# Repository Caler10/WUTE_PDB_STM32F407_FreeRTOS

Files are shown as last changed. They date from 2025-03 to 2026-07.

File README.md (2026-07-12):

# 针对WUTE车队电动方程式赛车开发的智能低压配电板 PDB

# 关于本项目

一款本人设计开发的基于STM32F4+FreeRTOS开发的智能低压配电板(PDB,Power Delivery Board)，具体功能如下：

1. 支持多路低压配电过流保护与诊断（基于智能高边驱动芯片，取代保险丝）
2. 支持对接入设备实现配电控制与管理，实现智能化配电功能（基于智能高边驱动芯片，取代继电器）
3. 负责赛车车身风扇、水泵、尾灯、蜂鸣器、DRS等设备的控制
4. 接收并解析来自VCU的配电CAN报文指令和来自仪表的DRS启停CAN报文，同时发送各路配电诊断数据、各车身设备启停状态至CAN总线
5. 集成DCDC继电器、激活继电器
6. 支持过流保护、反接保护、TVS保护、过压保护等多项安全功能

# 设计说明

## 硬件说明

因整车低压配电需要的载流较大，担心智能低压配电板由于设计缺陷导致需要重新设计和打板，为降低开发成本，驱动电路和控制电路采用分板设计（核心板+底板）

智能低压配电板架构图如下：

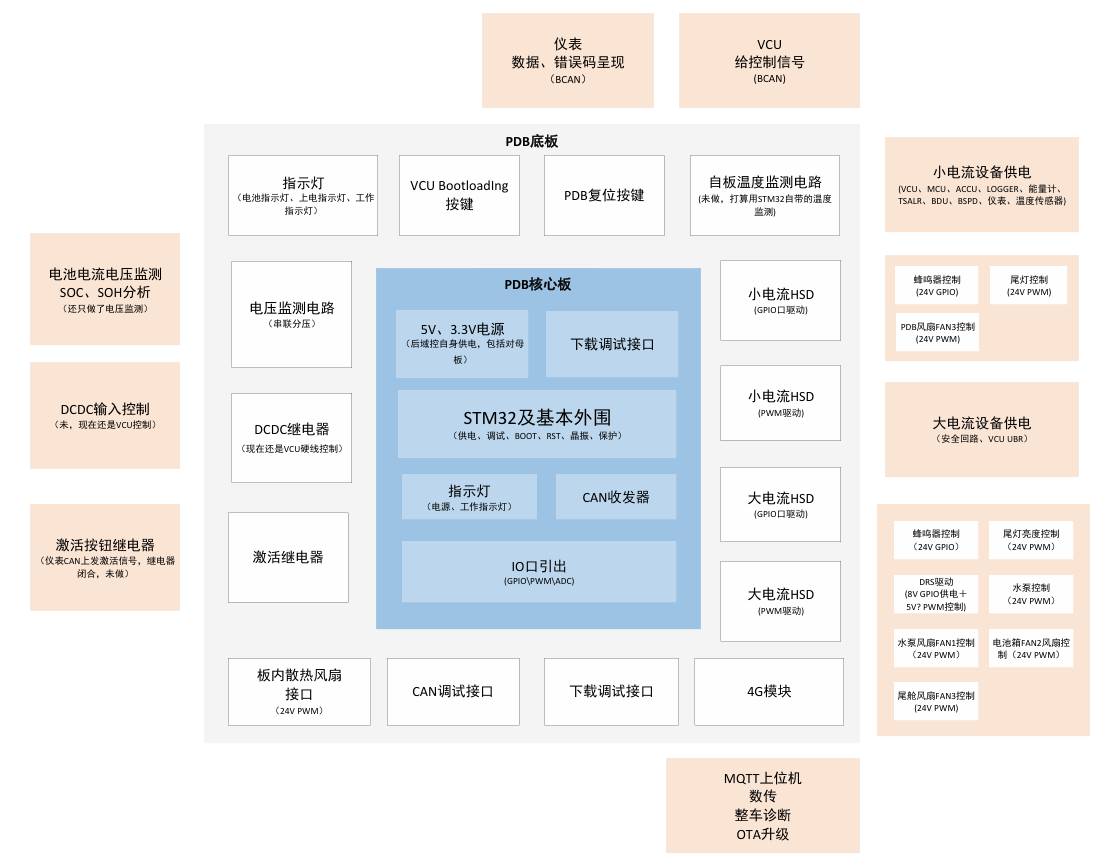
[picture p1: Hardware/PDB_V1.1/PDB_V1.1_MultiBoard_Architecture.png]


### PDB叠板设计

该项目硬件采用Altium Designer开发，PDB的核心板和底板之间采用板对板连接器连接

PDB_V1.0集成了OLED实时诊断数据显示，但是观察灵活性不够，因此PDB_V1.1取消了OLED，集成了4G数传功能，方便远程监测赛车配电情况，另外PDB_V1.1在底板增加了烧录、CAN调试接口，并优化了配电载流走线、修复了一些器件PCB封装问题

PDB_V1.0_MultiBoard：

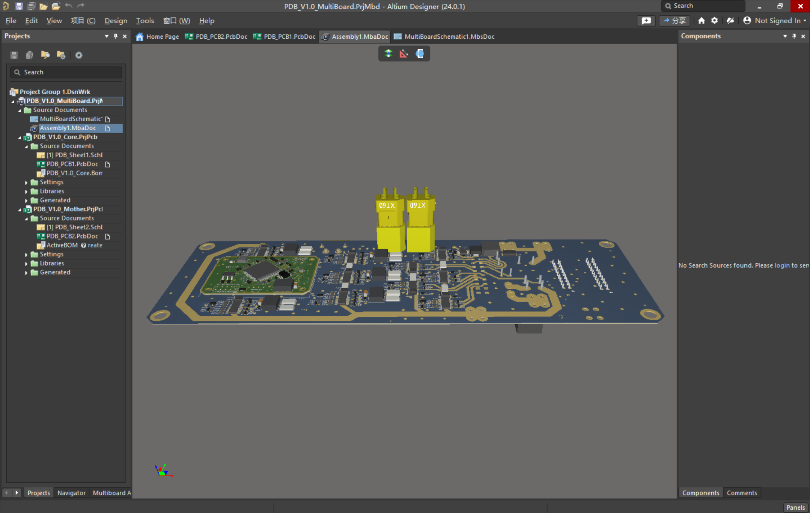
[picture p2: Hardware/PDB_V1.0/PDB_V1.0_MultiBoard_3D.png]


PDB_V1.1_MultiBoard：

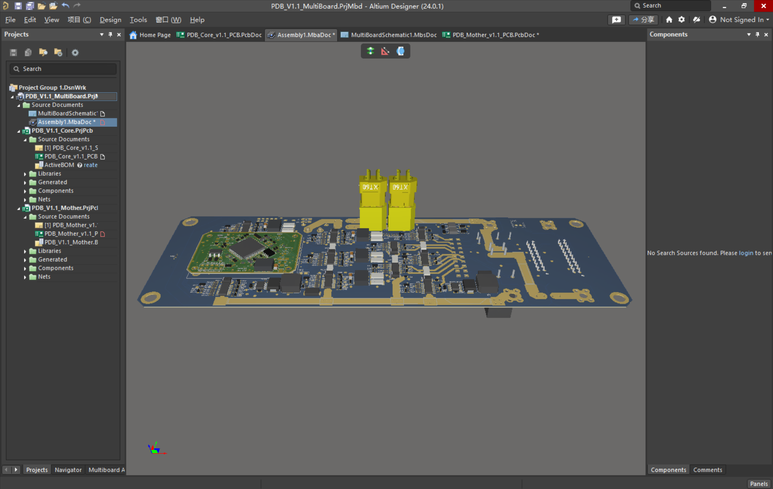
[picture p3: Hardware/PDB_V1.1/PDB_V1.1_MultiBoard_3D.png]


### PDB核心板设计

PDB_V1.0核心板：

V1.0核心板支持外接OLED，实现诊断数据实时显示

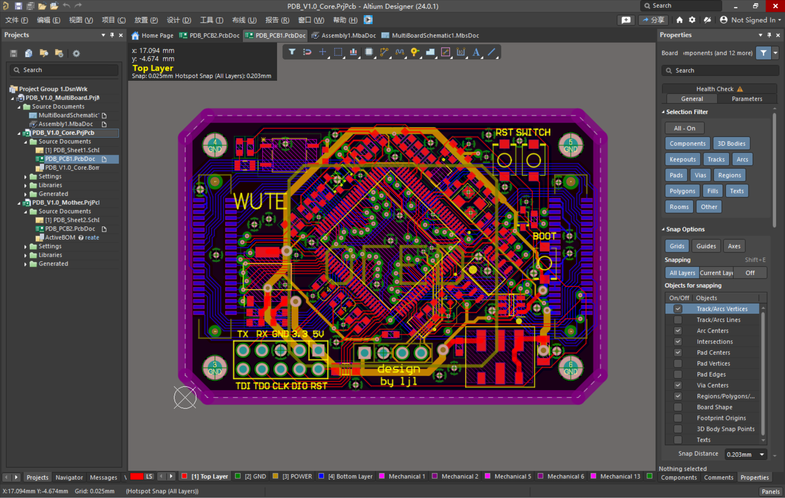
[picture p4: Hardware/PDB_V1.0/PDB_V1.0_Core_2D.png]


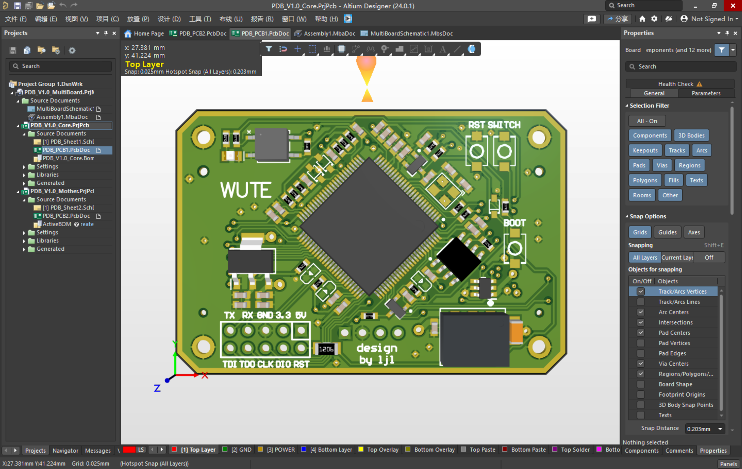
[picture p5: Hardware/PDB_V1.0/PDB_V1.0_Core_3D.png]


PDB_V1.1核心板：

V1.1核心板为兼容4G模块增加了3.3V至1.8V的电平转换模块，同时取消了OLED接口，另外相比V1.0版本增加了过流保护和反接保护电路

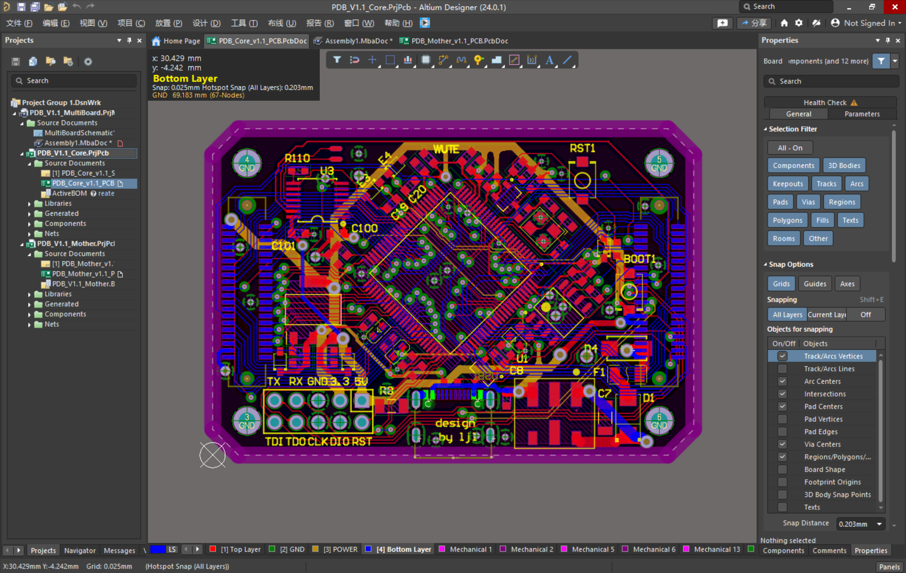
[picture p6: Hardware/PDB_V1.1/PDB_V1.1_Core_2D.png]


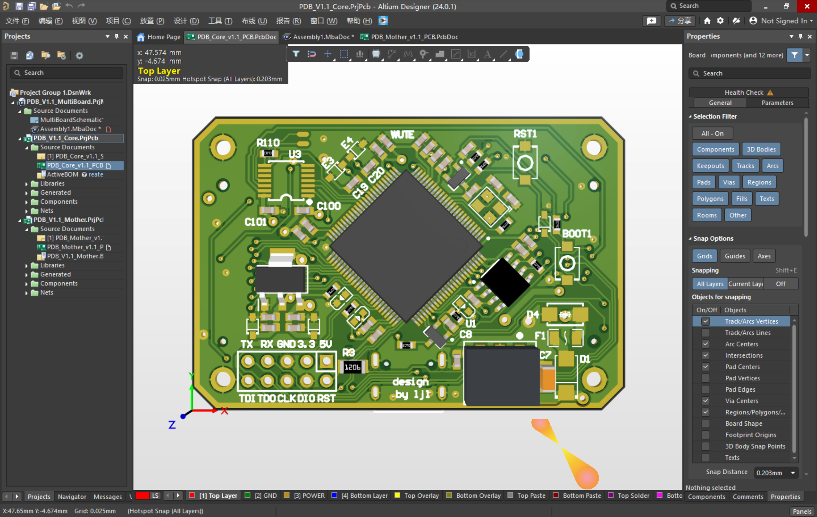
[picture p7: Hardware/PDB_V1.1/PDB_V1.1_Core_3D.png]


### PDB底板设计

PDB_V1.0底板：

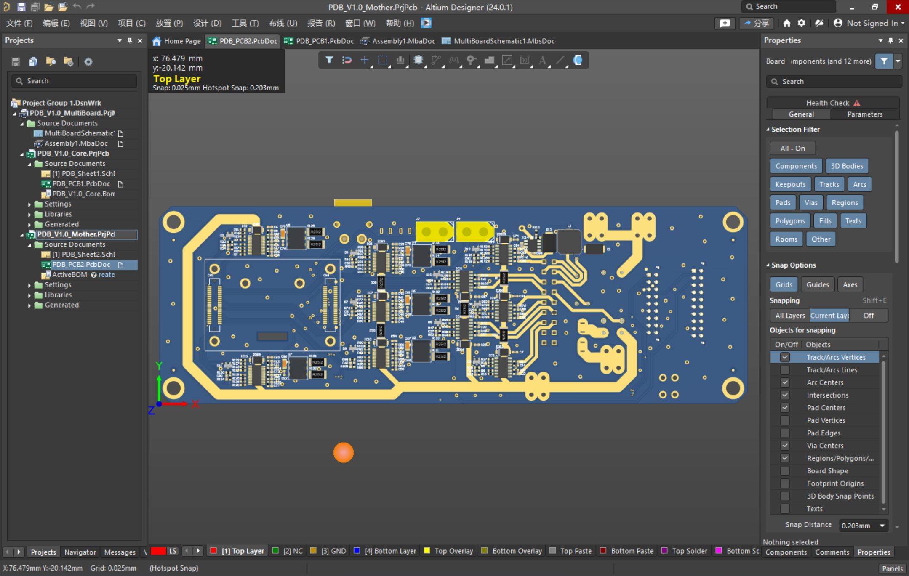
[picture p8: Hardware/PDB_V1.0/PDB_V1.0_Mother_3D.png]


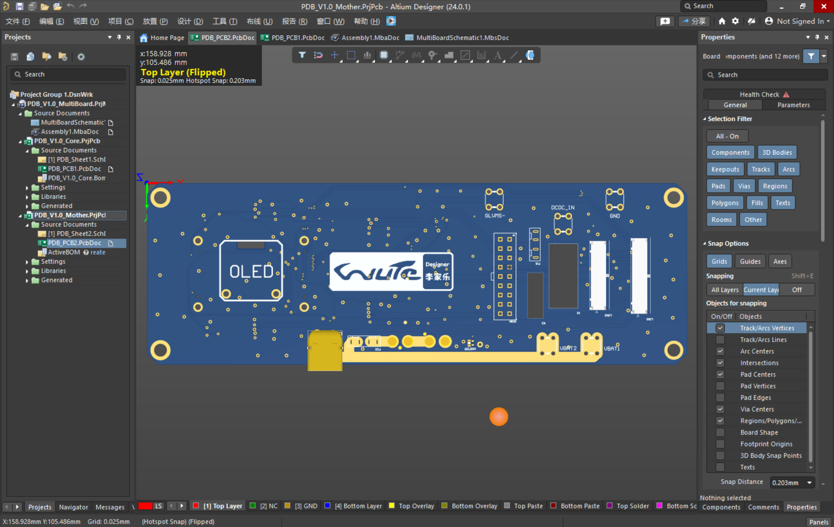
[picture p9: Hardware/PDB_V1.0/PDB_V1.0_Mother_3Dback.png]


PDB_V1.1底板：

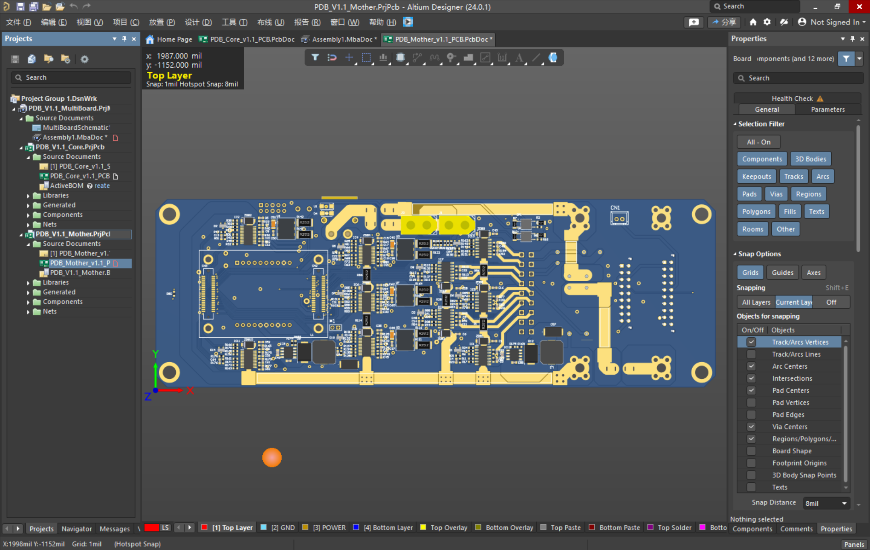
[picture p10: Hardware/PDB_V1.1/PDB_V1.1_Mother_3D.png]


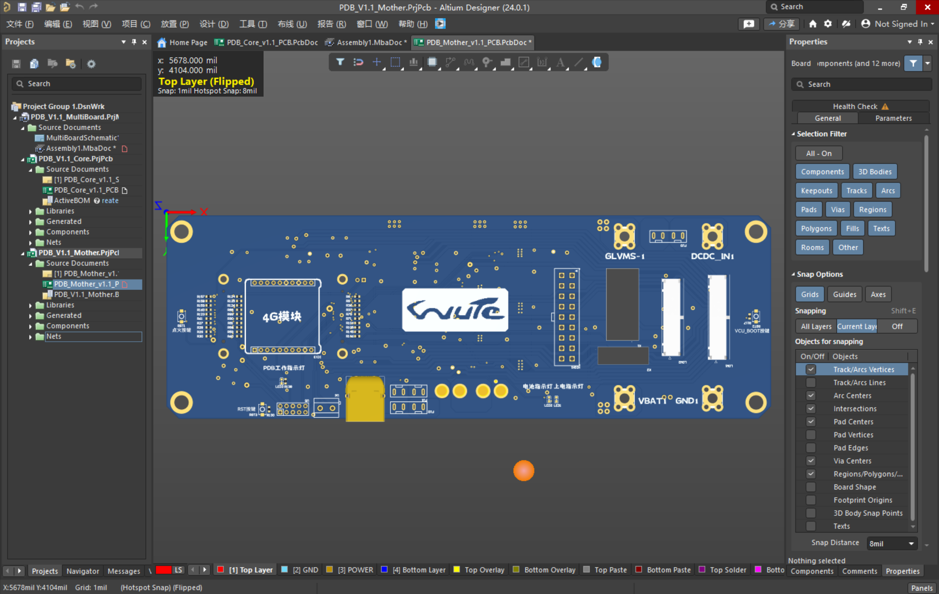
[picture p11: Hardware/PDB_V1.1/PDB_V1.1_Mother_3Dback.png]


## 软件说明

开发平台：STM32F407VET6

开发环境：STM32cubeMX+Keil

软件架构：基于CORE层+BSP层+FreeRTOS+APP层的架构开发

软件功能：

1. 智能高边驱动芯片HSD集群GPIO/PWM驱动
   
2. HSD诊断脚ADC+DMA中断采集与诊断分析
   
3. OLED IIC驱动与诊断可视化
   
4. CAN报文中断接收解析与诊断信息定时发送
   
5. 基于事件组/信号量/队列的任务间通信等

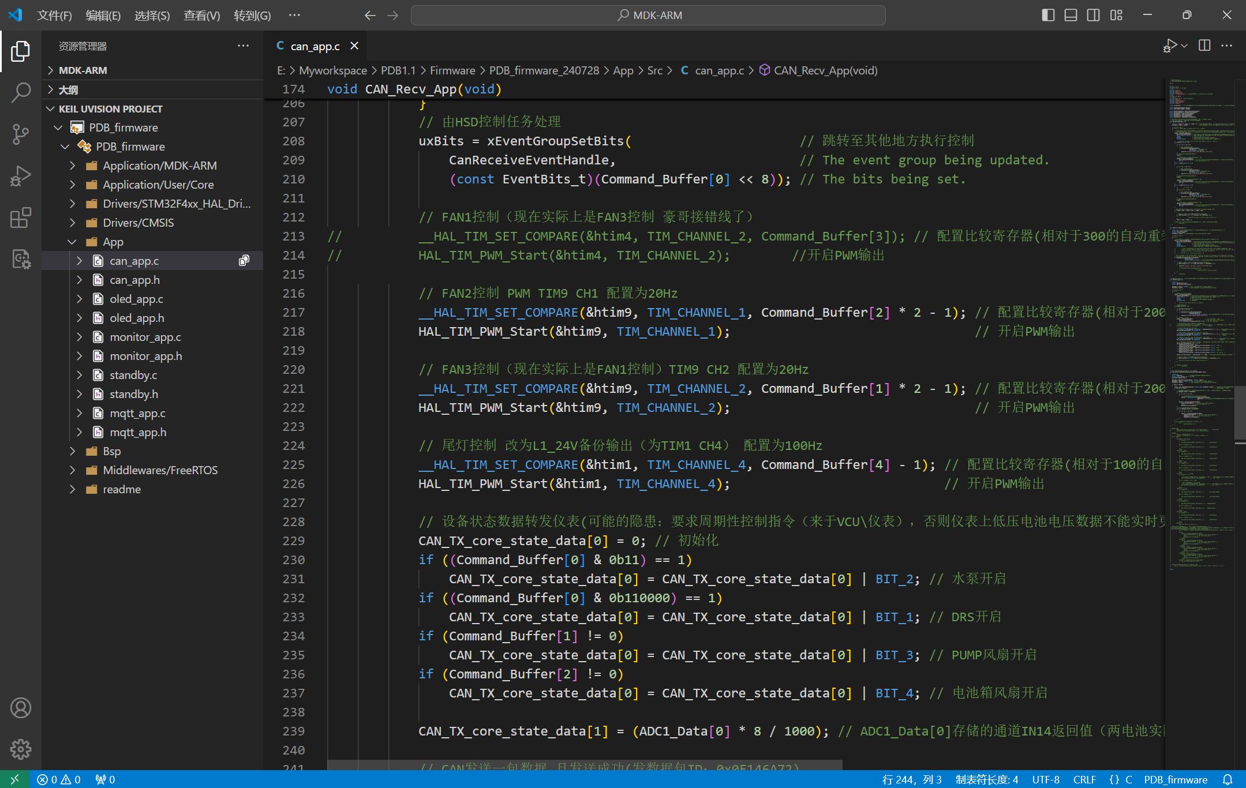
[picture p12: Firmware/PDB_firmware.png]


# 项目成果

该项目顺利完成开发并搭载在2024赛季E10赛车上，通过了累计50+小时的耐久测试，有效保障赛车低压系统配电安全同时实现了整车轻量化（采用HSD取代保险丝和继电器，实现配电盒整体减重约30%），并支撑E10赛车在2024年FSAE中国大学生电动方程式汽车大赛顺利完赛并取得全国季军。

智能低压配电板PDB实物图：



PDB和两块低压电池集成封装，布置在赛车尾部



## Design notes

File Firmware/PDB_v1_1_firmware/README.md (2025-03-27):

MX生成FreeRTOS版本（后面还有一个自己移植FreeRTOS版本）

由于电池VBAT始终向PDB供电，所以单片机不会关机，考虑读取PA0(上GLVMS为高，下GLVMS为低电平)

软件流程

当处于休眠时，监测到PA0上升沿唤醒

初始化阶段：
RST、上电后如果PA0读取非高电平（后可加其他条件，如CAN开始无应答、监听时），1分钟后进入休眠
如果PA0为高电平
    OLED开机界面启动
    CAN中断读取启动
    HSD所有输出开启
    OLED退出开机界面，进入指示状态

进入任务调度
    HSD1、HSD2诊断与分析（定时执行）[两队列：传出HSD诊断数据、报警信号；两事件：一出现报警信息，数据传输事件]（报过警的不丢,也显示，但说明过去式）
    电压监测与分析（定时执行）[两队列：电压监测数据、报警信号；两事件：一出现报警信息，数据传输事件]
    OLED监视（HSD电流检测数据来临事件启动）[收事件]
    CAN发送（HSD电流检测数据来临事件启动）[收事件]
    CAN接收（消息来临标志位启动）[收]
    HSD通道启停控制（CAN接收控制信号事件启动）[]
    DRS控制（CAN接收控制信号事件启动）[]
    准备与取消准备休眠（PA0 GPIO中断读取，为低电平后OLED指示将1分钟后进入休眠，当PA0回高电平时退出准备）[]
    休眠（由进入休眠事件启动，为低电平后倒计时1分钟后关闭LED、OLED，将PA0复用为唤醒引脚，配置寄存器进入休眠）[]

疑问：
有什么方式实现报警发过了不再发？
现在CAN接收标准帧和拓展帧都能收？

为什么OLED字符、图片数组声明、定义前要加const使其常数化（但是加了传入画图片函数里时会警告，所以去掉了）
小心多个任务读取同一个事件位时，一个读完了把厕所炸了其他的就上不了了

MX生成FreeRTOS的使用:
大部分FreeRTOS功能函数还要include对应文件后才能使用

HSD1handledEvent：存放HSD1组的完成诊断的相对输出口数据

CAN发尾灯信号，PDB控制
// 整合电压电流采集的两数据（数组）二维数组转一维数组，参考https://blog.csdn.net/m0_54158068/article/details/124275490

//有的地方set事件改为清理事件
uxBits = xEventGroupClearBits(
                                xEventGroup,  /* The event group being updated. */
                                BIT_0 | BIT_4 );/* The bits being cleared. */

  if( ( uxBits & ( BIT_0 | BIT_4 ) ) == ( BIT_0 | BIT_4 ) )
  {
      /* Both bit 0 and bit 4 were set before xEventGroupClearBits()
      was called.  Both will now be clear (not set). */
  }
  else if( ( uxBits & BIT_0 ) != 0 )
  {
      /* Bit 0 was set before xEventGroupClearBits() was called.  It will
      now be clear. */
  }
  else if( ( uxBits & BIT_4 ) != 0 )
  {
      /* Bit 4 was set before xEventGroupClearBits() was called.  It will
      now be clear. */
  }
  else
  {
      /* Neither bit 0 nor bit 4 were set in the first place. */
  }

20240524：
比20240413版本
解决了风扇无法控制的问题（CAN中断接收到后不能将数据完整地压入队列供CAN_Reseive函数接收处理）
取消诊断、诊断数据打包发送、错误发送功能（控制功耗）
删除CPU占用监测任务

20240704：
实现DRS的驱动
可以正常使用版本

20240728：
更新PDB指令报文的接收
实现尾灯、风扇PWM控制
PDB设备状态数据上CAN（给仪表）
实现惯导转发上CAN
实现4G模块驱动

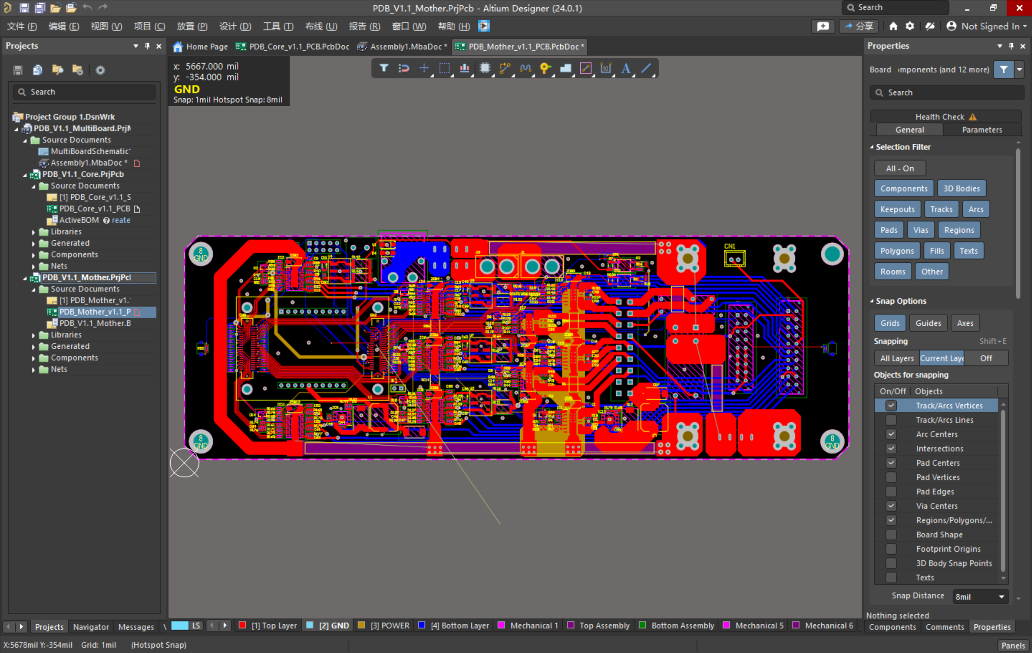
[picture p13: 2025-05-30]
Hardware/PDB_V1.1/PDB_V1.1_Mother_2D.png

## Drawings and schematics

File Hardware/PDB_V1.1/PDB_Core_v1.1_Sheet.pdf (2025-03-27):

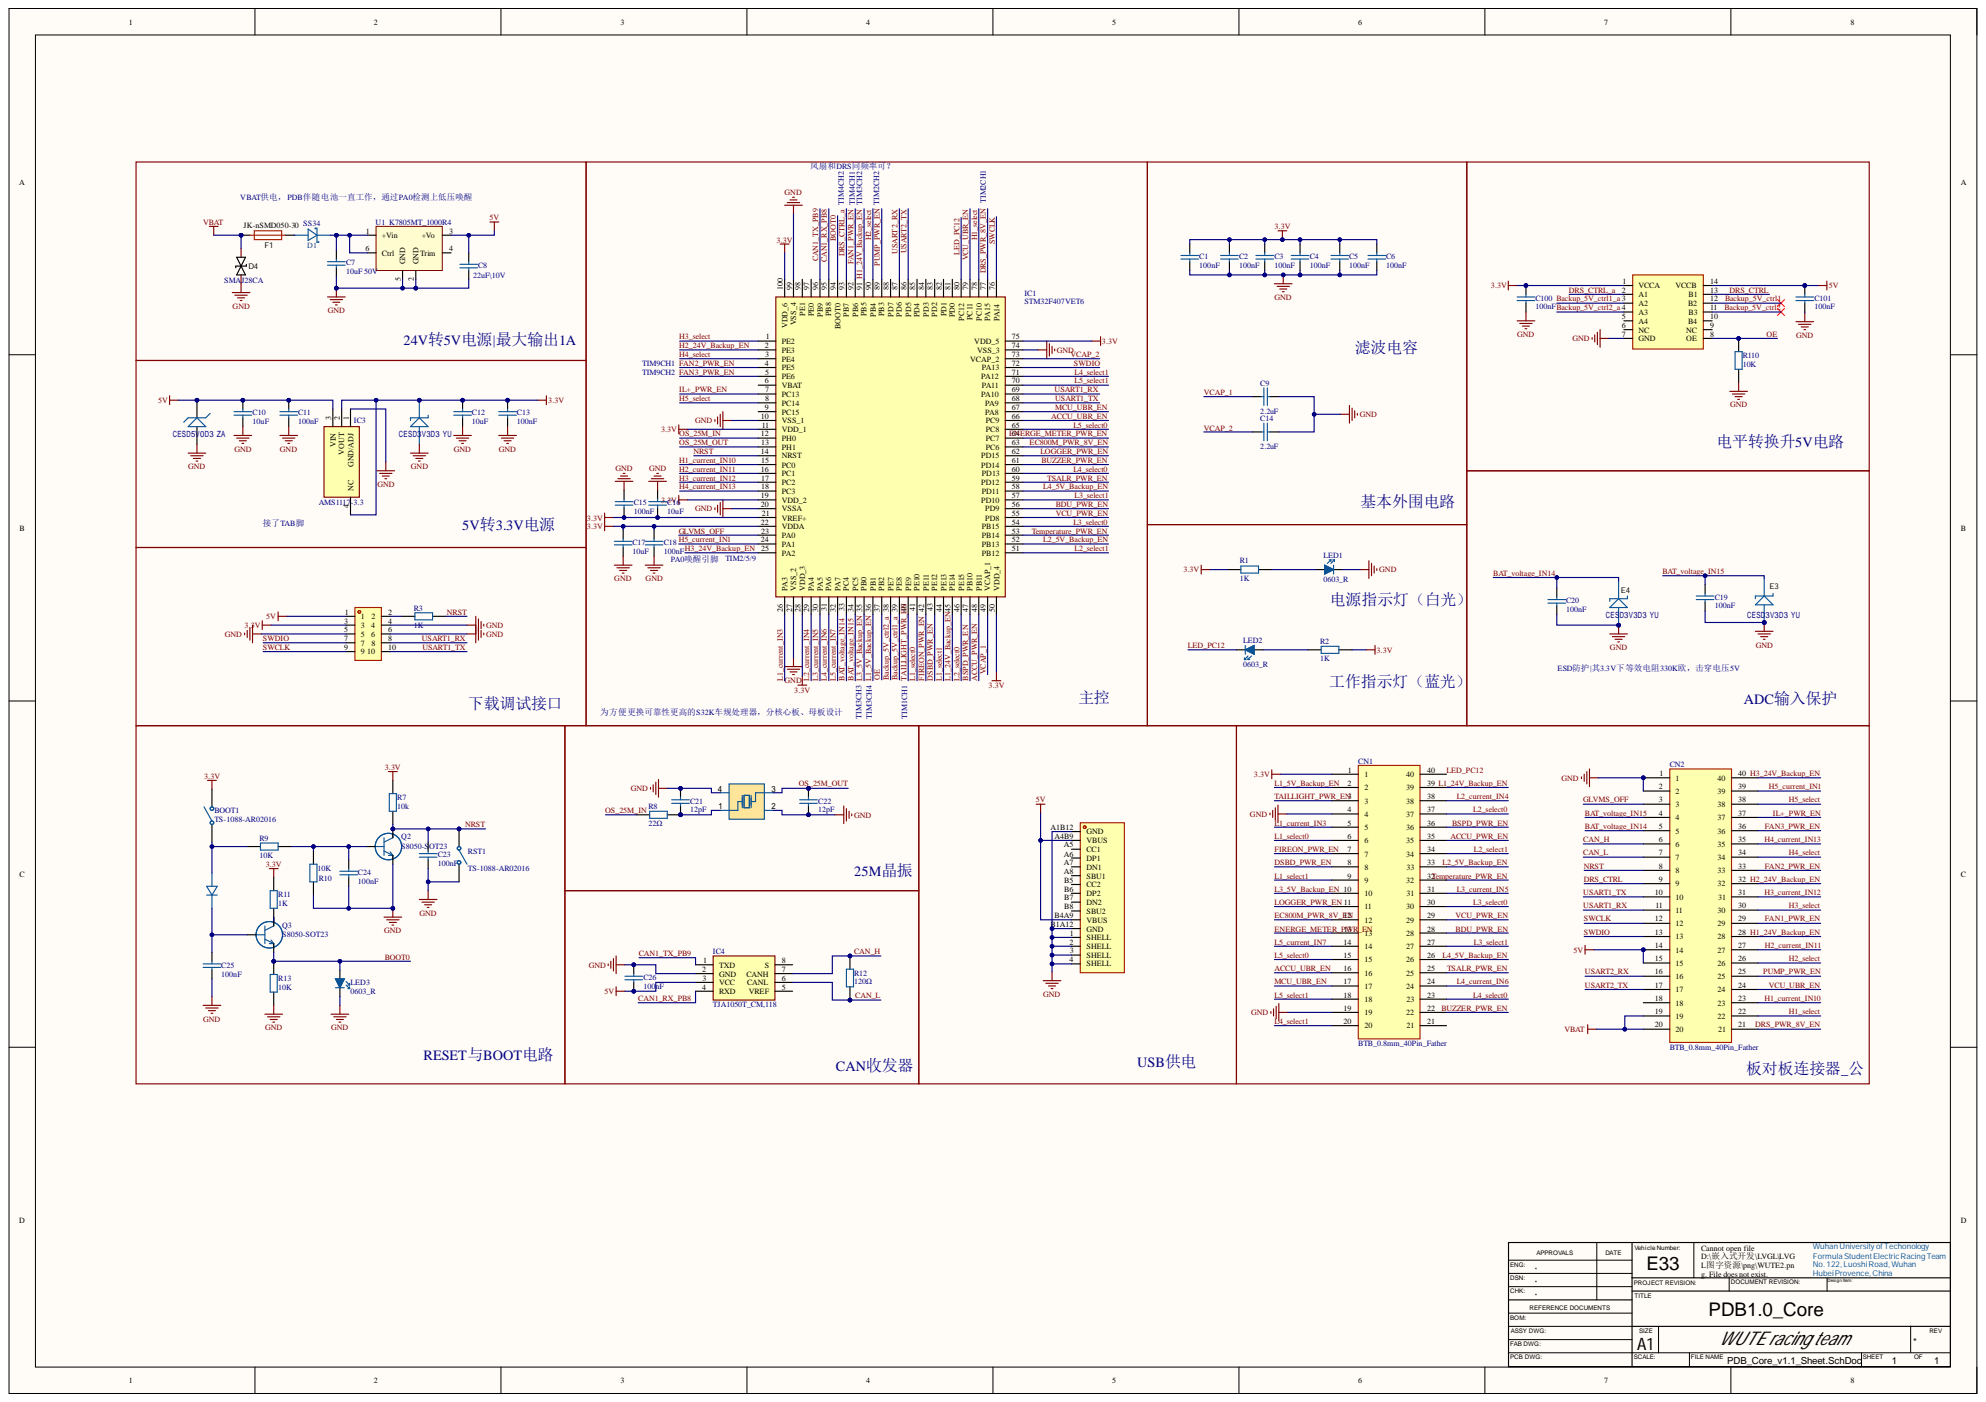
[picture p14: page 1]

GND/ADJ 1 VOUT 2 VIN 3 NC 4

接了 脚 TAB | | | 转 电 源 V 3 . 3 V

下载调试 | 接 口

3.3V 3.3V 电 路 BOOT | 100nF R8 2 5 M 晶 振 | 5V 供 电 USB | | | 器 公 _

A P PRO VA L S | DAT E | Ve h i c l e Nu m b e r : E3 3 | C annot open file W u h a n Un ive rsity of T ech o n o l o g y 嵌入式开发 F o r m u l a Stu d e nt E l ectr ic Raci n g T e a m D:\ \ LVGL\LVG L 图字资源 \png\WUT E2.pn No. 1 2 2, L u osh iRo a d, W u h a n g. File doe s not exist. Hu b e i P r ove nce, Ch i n a

ENG :
** DSN: | | PRO J ECT RE VISION: | DOCUM ENT RE VISION: | D esi g n I t e m :
CHK : * | | TIT L E PDB1.0 _Core

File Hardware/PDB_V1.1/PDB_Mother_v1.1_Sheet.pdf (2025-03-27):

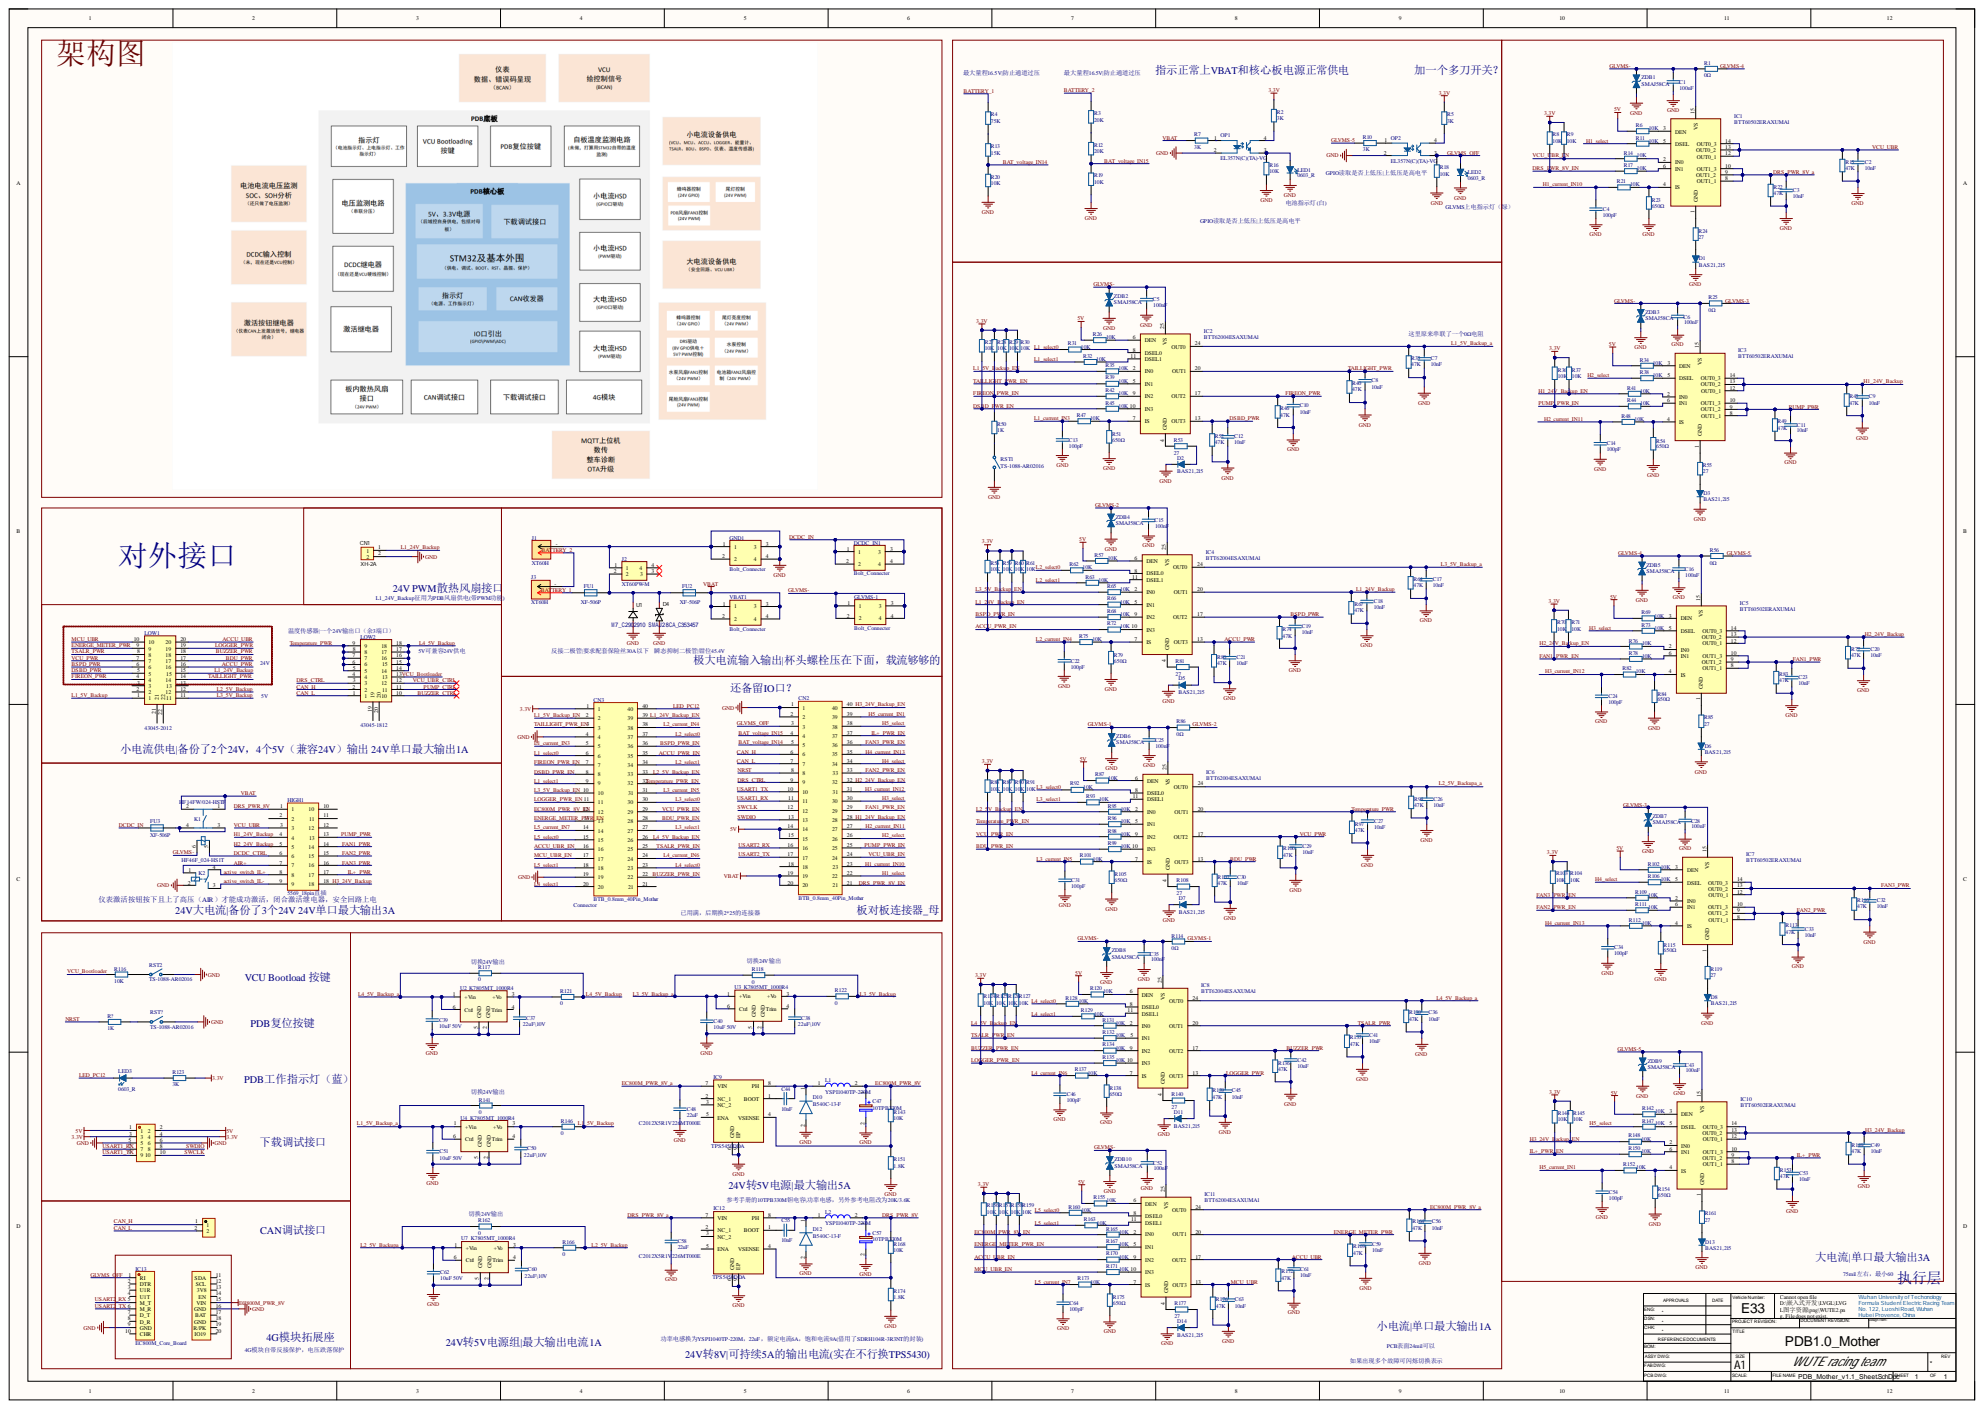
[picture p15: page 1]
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

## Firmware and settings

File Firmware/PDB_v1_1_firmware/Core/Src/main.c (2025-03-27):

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
/* Includes ------------------------------------------------------------------*/
#include "main.h"
#include "cmsis_os.h"
#include "adc.h"
#include "can.h"
#include "dma.h"
#include "tim.h"
#include "usart.h"
#include "gpio.h"

/* USER CODE BEGIN Includes */
//bsp
#include "hsd_drive.h"
#include "mycan.h"
#include "oled.h"
#include "oledfont.h"	
#include "myusart.h"
#include "voltage_monitor.h"
//app
#include "can_app.h"
#include "oled_app.h"
/* USER CODE END Includes */


void SystemClock_Config(void);
void MX_FREERTOS_Init(void);
/* USER CODE BEGIN 0 */
//分析32位bit数呈现为二进制时1的个数
int count_one_bits(unsigned int value)
{
  int count = 0;
  while (value)
  {
    value &= (value - 1);// 
    count++;
  }
  return count;
} 

/* USER CODE END 0 */

/**
  * @brief  The application entry point.
  * @retval int
  */
int main(void)
{
  /* MCU Configuration--------------------------------------------------------*/

  /* Reset of all peripherals, Initializes the Flash interface and the Systick. */
  HAL_Init();

  /* Configure the system clock */
  SystemClock_Config();

  /* Initialize all configured peripherals */
  MX_GPIO_Init();
  MX_DMA_Init();
  MX_ADC1_Init();
  MX_ADC2_Init();
  MX_ADC3_Init();
  MX_CAN1_Init();
  MX_USART1_UART_Init();
  MX_TIM3_Init();
  MX_TIM6_Init();
  MX_TIM4_Init();
  MX_USART2_UART_Init();
  MX_TIM1_Init();
  MX_TIM9_Init();
  MX_TIM2_Init();
  /* Init scheduler */
  osKernelInitialize();

  /* Call init function for freertos objects (in freertos.c) */
  MX_FREERTOS_Init();

  /* Start scheduler */
  osKernelStart();

  /* We should never get here as control is now taken by the scheduler */
  /* Infinite loop */
  /* USER CODE BEGIN WHILE */
//	HAL_GPIO_WritePin(GPIOE, GPIO_PIN_6, 1);		//DRS_PWR_8V_EN
  while (1)
  {
    /* USER CODE END WHILE */

    /* USER CODE BEGIN 3 */
  }
  /* USER CODE END 3 */
}

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
/**
  * @brief  Period elapsed callback in non blocking mode
  * @note   This function is called  when TIM14 interrupt took place, inside
  * HAL_TIM_IRQHandler(). It makes a direct call to HAL_IncTick() to increment
  * a global variable "uwTick" used as application time base.
  * @param  htim : TIM handle
  * @retval None
  */
void HAL_TIM_PeriodElapsedCallback(TIM_HandleTypeDef *htim)
{
  if (htim->Instance == TIM14) {
    HAL_IncTick();
  }
}

/**
  * @brief  This function is executed in case of error occurrence.
  * @retval None
  */
void Error_Handler(void)
{
  /* USER CODE BEGIN Error_Handler_Debug */
  /* User can add his own implementation to report the HAL error return state */
  __disable_irq();
  while (1)
  {
  }
  /* USER CODE END Error_Handler_Debug */
}

#ifdef  USE_FULL_ASSERT
/**
  * @brief  Reports the name of the source file and the source line number
  *         where the assert_param error has occurred.
  * @param  file: pointer to the source file name
  * @param  line: assert_param error line source number
  * @retval None
  */
void assert_failed(uint8_t *file, uint32_t line)
{
  /* USER CODE BEGIN 6 */
  /* User can add his own implementation to report the file name and line number,
     ex: printf("Wrong parameters value: file %s on line %d\r\n", file, line) */
  /* USER CODE END 6 */
}
#endif /* USE_FULL_ASSERT */

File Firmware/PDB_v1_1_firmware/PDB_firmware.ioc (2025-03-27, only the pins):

Mcu.UserName=STM32F407VETx
PA0-WKUP.Signal=GPXTI0
PA1.Signal=ADCx_IN1
PA10.Signal=USART1_RX
PA11.Signal=GPIO_Output
PA12.Signal=GPIO_Output
PA13.Signal=SYS_JTMS-SWDIO
PA14.Signal=SYS_JTCK-SWCLK
PA15.Signal=GPIO_Output
PA3.Signal=ADCx_IN3
PA4.Signal=ADCx_IN4
PA5.Signal=ADCx_IN5
PA6.Signal=ADCx_IN6
PA7.Signal=ADCx_IN7
PA8.Signal=GPIO_Output
PA9.Signal=USART1_TX
PB0.Signal=GPIO_Output
PB1.Signal=GPIO_Output
PB10.Signal=GPIO_Output
PB11.Signal=GPIO_Output
PB12.Signal=GPIO_Output
PB13.Signal=GPIO_Output
PB14.Signal=GPIO_Output
PB15.Signal=GPIO_Output
PB2.Signal=GPIO_Output
PB3.Signal=S_TIM2_CH2
PB4.Signal=GPIO_Output
PB5.Signal=GPIO_Output
PB6.Signal=GPIO_Output
PB7.Signal=S_TIM4_CH2
PC0.Signal=ADCx_IN10
PC1.Signal=ADCx_IN11
PC10.Signal=GPIO_Output
PC11.Signal=GPIO_Output
PC12.Signal=GPIO_Output
PC13-ANTI_TAMP.Signal=GPIO_Output
PC14-OSC32_IN.Signal=GPIO_Output
PC2.Signal=ADCx_IN12
PC3.Signal=ADCx_IN13
PC4.Signal=ADCx_IN14
PC5.Signal=ADCx_IN15
PC6.Signal=GPIO_Output
PC7.Signal=GPIO_Output
PC8.Signal=GPIO_Output
PC9.Signal=GPIO_Output
PD0.Signal=CAN1_RX
PD1.Signal=CAN1_TX
PD10.Signal=GPIO_Output
PD11.Signal=GPIO_Output
PD12.Signal=GPIO_Output
PD13.Signal=GPIO_Output
PD14.Signal=GPIO_Output
PD15.Signal=GPIO_Output
PD5.Signal=USART2_TX
PD6.Signal=USART2_RX
PD8.Signal=GPIO_Output
PD9.Signal=GPIO_Output
PE0.Signal=GPIO_Output
PE1.Signal=GPIO_Output
PE10.Signal=GPIO_Output
PE11.Signal=GPIO_Output
PE12.Signal=GPIO_Output
PE13.Signal=GPIO_Output
PE14.Signal=S_TIM1_CH4
PE15.Signal=GPIO_Output
PE2.Signal=GPIO_Output
PE3.Signal=GPIO_Output
PE4.Signal=GPIO_Output
PE5.Signal=S_TIM9_CH1
PE6.Signal=S_TIM9_CH2
PE7.Signal=GPIO_Output
PE8.Signal=GPIO_Output
PE9.Signal=GPIO_Output
PH0-OSC_IN.Signal=RCC_OSC_IN
PH1-OSC_OUT.Signal=RCC_OSC_OUT

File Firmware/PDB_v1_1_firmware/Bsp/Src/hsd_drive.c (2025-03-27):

// hsd的基本驱动函数，供上层应用调用
#if 1

#include "gpio.h" //各引脚控制
#include "adc.h"  //有用到ADC DMA
#include "hsd_drive.h"
#include "myusart.h"

/*
 * 小电流HSD:
 * HSD诊断规则：DEN为0失能诊断，IS高阻抗；EN且被片选选中，开始对应检测	疑问：延时？
 * 诊断DSEL真值表：00-OUT0 01-OUT1 10-OUT2 11-OUT3
 * IS失效情况：与GND短路、限流、过压、动态温升过度或开路、负载关闭
 */

/*
引脚映射：
L1_select0 -> PE10
L1_select1 -> PE13
L1_5V_Backup_EN -> PB1
TAILLIGHT_PWR_EN -> PE9（默认关闭）! 现在改为了PE14(L1 24V输出)
FIREON_PWR_EN -> PE11
DSBD_PWR_EN -> PE12
L1_current_IN3 -> PA3

L2_select0 -> PE15
L2_select1 -> PB12
L3_5V_Backup_EN -> PB0
L1_24V_Backup_EN -> PE14
BSPD_PWR_EN -> PB10
ACCU_PWR_EN -> PB11
L2_current_IN4 -> PA4

L3_select0 -> PB15
L3_select1 -> PD10
L2_5V_Backup_EN -> PB13
Temperature_PWR_EN -> PB14
VCU_PWR_EN -> PD8
BDU_PWR_EN -> PD9
L3_currrent_IN5 -> PA5

L4_select0 -> PD13
L4_select1 -> PA12
L4_5V_Backup_EN -> PD11!
TSALR_PWR_EN -> PD12!
BUZZER_PWR_EN -> PD14（默认关闭）
LOGGER_PWR_EN -> PD15
L4_current_IN6 -> PA6


L5_select0 -> PC8
L5_select1 -> PA11
EC800M_PWR_8V_EN -> PC6
ENERGE_METER_PWR_EN -> PC7
ACCU_UBR_EN -> PC9
MCU_UBR_EN -> PA8
L5_current_IN7 -> PA7

H1_select -> PC10
VCU_UBR_EN -> PC11
DRS_PWR_8V_EN -> PA15
H1_current_IN10 -> PC0

H2_select -> PB4
H1_24V_Backup_EN -> PB5!
PUMP_PWR_EN -> PB3（默认关闭）
H2_current_IN11 -> PC1

H3_select -> PE2
H2_24V-Backup_EN -> PE3!
FAN1_PWR_EN -> PB6（默认关闭）
H3_current_IN12 -> PC2

H4_select -> PE4
FAN3_PWR_EN -> PE6（默认关闭）
FAN2_PWR_EN -> PE5（默认关闭）
H4_current_IN13 -> PC3

H5_select -> PC14
H3_24V_Backup_EN -> PA2
IL+_PWR_EN -> PC13!
H5_current_IN1 -> PA1

 */

// 为什么数组多1单元，留一单元告知相对HSD编号数（可换更好方法）
uint16_t ADC2_Data[5]; // 存放ADC2原始读取值和处理后的小电流HSD监测电流值（实际电流*10），最后压缩格式整合到AV_Data[32]数组中
uint16_t ADC3_Data[5]; // 存放ADC3原始读取值和处理后的大电流HSD监测电流值（实际电流*10），最后压缩格式整合到AV_Data[32]数组中
uint8_t now_HSD1_channelx;
uint8_t now_HSD2_channelx;
/*故障协议:
0x10:过流故障且已消除		0x11:过流故障未消除
0x20:..
*/

// 实现对所有HSD所有输出口输出使能、失能的控制
void HSD_Output_Enable_HSDs(uint8_t HSD_PinState)
{
	// 小电流HSD
	HAL_GPIO_WritePin(GPIOB, GPIO_PIN_1, HSD_PinState);	 	//L1_5V_Backup_EN
	HAL_GPIO_WritePin(GPIOE, GPIO_PIN_9, HSD_PinState);		//TAILLIGHT_PWR_EN（未使用，作备份输出）
	HAL_GPIO_WritePin(GPIOE, GPIO_PIN_11, HSD_PinState);		//FIREON_PWR_EN
	HAL_GPIO_WritePin(GPIOE, GPIO_PIN_12, HSD_PinState);	//DSBD_PWR_EN

	HAL_GPIO_WritePin(GPIOB, GPIO_PIN_0, HSD_PinState);		//L3_5V_Backup_EN
//	HAL_GPIO_WritePin(GPIOE, GPIO_PIN_14, HSD_PinState);	//L1_24V_Backup_EN（征用为尾灯控制，但改为了PWM）
	HAL_GPIO_WritePin(GPIOB, GPIO_PIN_10, HSD_PinState);	//BSPD_PWR_EN
	HAL_GPIO_WritePin(GPIOB, GPIO_PIN_11, HSD_PinState);	//ACCU_PWR_EN

	HAL_GPIO_WritePin(GPIOB, GPIO_PIN_13, HSD_PinState);	//L2_5V_Backup_EN
	HAL_GPIO_WritePin(GPIOB, GPIO_PIN_14, HSD_PinState);	//Temperature_PWR_EN
	HAL_GPIO_WritePin(GPIOD, GPIO_PIN_8, HSD_PinState);	//VCU_PWR_EN
	HAL_GPIO_WritePin(GPIOD, GPIO_PIN_9, HSD_PinState);	//BDU_PWR_EN

	HAL_GPIO_WritePin(GPIOD, GPIO_PIN_11, HSD_PinState);		//L4_5V_Backup_EN
	HAL_GPIO_WritePin(GPIOD, GPIO_PIN_12, HSD_PinState);	//TSALR_PWR_EN
	HAL_GPIO_WritePin(GPIOD, GPIO_PIN_14, HSD_PinState);	//BUZZER_PWR_EN
	HAL_GPIO_WritePin(GPIOD, GPIO_PIN_15, HSD_PinState);	//LOGGER_PWR_EN

	HAL_GPIO_WritePin(GPIOC, GPIO_PIN_6, HSD_PinState);	//EC800M_PWR_8V_EN
	HAL_GPIO_WritePin(GPIOC, GPIO_PIN_7, HSD_PinState);	//ENERGE_METER_PWR_EN
	HAL_GPIO_WritePin(GPIOC, GPIO_PIN_9, HSD_PinState);		//ACCU_UBR_EN
	HAL_GPIO_WritePin(GPIOA, GPIO_PIN_8, HSD_PinState);		//MCU_UBR_EN

	// 大电流HSD
	HAL_GPIO_WritePin(GPIOC, GPIO_PIN_11, HSD_PinState);		//VCU_UBR_EN
	HAL_GPIO_WritePin(GPIOA, GPIO_PIN_15, HSD_PinState);	//DRS_PWR_8V_EN

	HAL_GPIO_WritePin(GPIOB, GPIO_PIN_5, HSD_PinState);		//H1_24V_Backup_EN
//	HAL_GPIO_WritePin(GPIOB, GPIO_PIN_3, HSD_PinState);		//PUMP_PWR_EN

	HAL_GPIO_WritePin(GPIOE, GPIO_PIN_3, HSD_PinState);		//H2_24V-Backup_EN
	HAL_GPIO_WritePin(GPIOB, GPIO_PIN_6, HSD_PinState);		//FAN1_PWR_EN（改为FAN3输出）

//	HAL_GPIO_WritePin(GPIOE, GPIO_PIN_6, HSD_PinState);		//FAN3_PWR_EN（改为FAN1输出，现PWM）
//	HAL_GPIO_WritePin(GPIOE, GPIO_PIN_5, HSD_PinState);		//FAN2_PWR_EN(现在PWM)

	HAL_GPIO_WritePin(GPIOA, GPIO_PIN_2, HSD_PinState);		//H3_24V_Backup_EN
	HAL_GPIO_WritePin(GPIOC, GPIO_PIN_13, HSD_PinState);	//IL+_PWR_EN
}

// 实现对每个HSD的输出使能、失能的单独控制
// HSDpin_number：每个输出口在所有HSD输出口中的绝对编号（=HSDx+HSD_OUTx,HSDx:0x10~0xA0,HSD_OUTx:0x01~0x03）
void HSD_Output_Enable_HSDPinx(uint8_t HSDpin_number, uint8_t HSD_PinState)
{

	uint8_t HSDx, HSD_OUTx;

	HSDx = HSDpin_number, HSDx = HSDx >> 4; // 获得HSD编号，如果编号是0x0则表示对所有HSD操作

	HSD_OUTx = HSDpin_number << 4, HSD_OUTx = HSD_OUTx >> 4;
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

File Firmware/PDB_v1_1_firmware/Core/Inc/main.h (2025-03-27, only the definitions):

#define BIT_0 1<<0		//HSD1通道1 ADC DMA处理完成	//CAN接收VCU回调接收到事件
#define BIT_1 1<<1		//HSD2通道2 ADC DMA处理完成	//CAN接收仪表回调接收到事件
#define BIT_2 1<<2		//HSD2通道3 ADC DMA处理完成  //
#define BIT_3 1<<3		//HSD2通道4 ADC DMA处理完成	//
#define BIT_4 1<<4		//HSD1 出现错误		//
#define BIT_5 1<<5		//HSD1 错误处理完成返回,继续		//
#define BIT_6 1<<6		//HSD1 一包数据分析完成	//
#define BIT_7 1<<7		//HSD1 一包数据上包完成,继续	//
#define BIT_8 1<<8		//HSD2通道1 ADC DMA处理完成	//
#define BIT_9 1<<9		//HSD2通道2 ADC DMA处理完成	//
#define BIT_10 1<<10	//HSD2 出现错误	//
#define BIT_11 1<<11	//HSD2 错误处理完成返回,继续	//
#define BIT_12 1<<12	//HSD2 一包数据分析完成	//
#define BIT_13 1<<13	//HSD2 一包数据上包完成,继续	//
#define BIT_14 1<<14	//BAT ADC DMA处理完成	//
#define BIT_15 1<<15	//BAT 出现错误	//
#define BIT_16 1<<16	//BAT 错误处理完成返回,继续		//
#define BIT_17 1<<17	//BAT 一包数据分析完成		//
#define BIT_18 1<<18	//BAT 一包数据上包完成,继续		//
#define BIT_19 1<<19  //	//
#define BIT_20 1<<20  //	//
#define BIT_21 1<<21	//		//
#define BIT_22 1<<22	//		//
#define BIT_23 1<<23	//OLED发CAN错误故障码		//设置为进待机标志位

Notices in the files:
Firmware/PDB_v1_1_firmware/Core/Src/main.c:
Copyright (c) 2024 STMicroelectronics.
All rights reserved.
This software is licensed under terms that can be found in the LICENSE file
